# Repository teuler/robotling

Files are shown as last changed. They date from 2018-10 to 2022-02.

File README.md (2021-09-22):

# robotling

"robotling" is a simple circuit board to control small robots. Check out the videos (videos [1](https://youtu.be/wil41YtIeN8), [2](https://youtu.be/cLstXW3RsBA), [3](https://www.youtube.com/watch?v=XF0T9Dlb07M), and with thermal camera, [4](https://youtu.be/qpSQO51BuJs), [5](https://youtu.be/tlYXab0FZrY)) and find the details in the German [wiki](https://github.com/teuler/robotling/wiki). 

<p align="center">
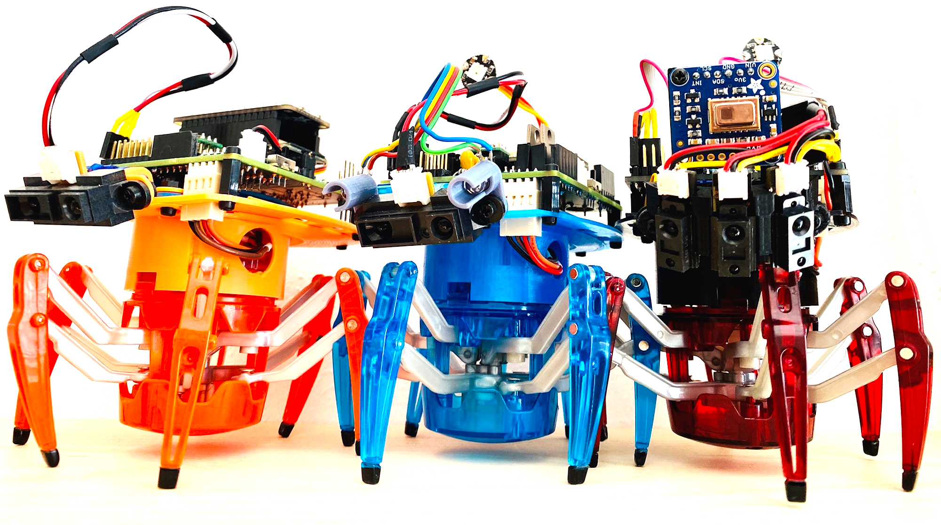
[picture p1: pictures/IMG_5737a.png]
  
</p>

### Release Notes

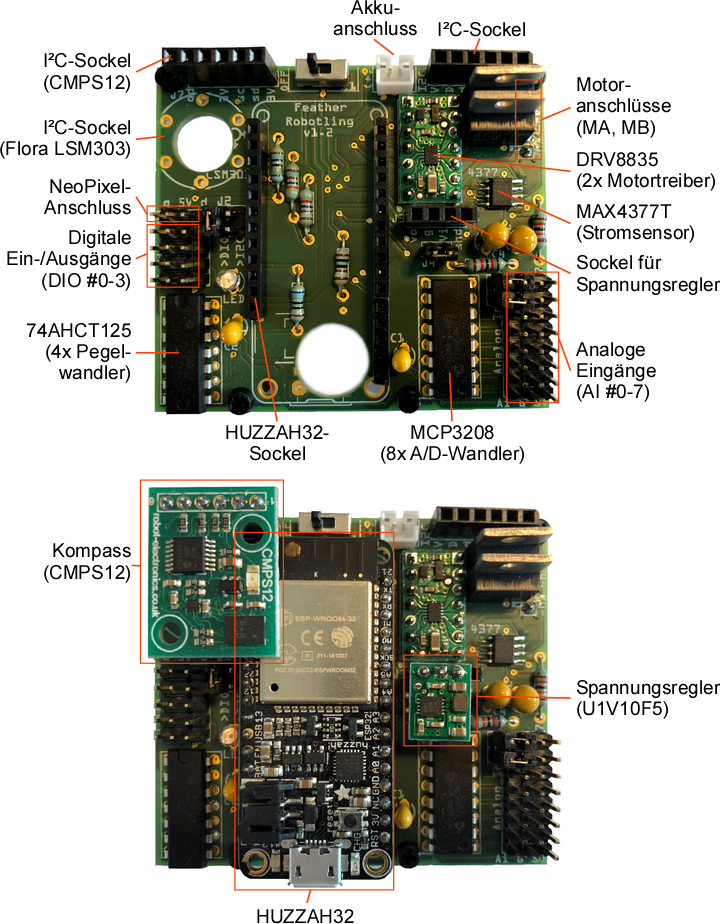
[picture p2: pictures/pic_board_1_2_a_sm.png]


* 2021-09-22
  - New firmware based on MicroPython v1.17 (w/`ulab`)
  - 
* 2021-05-02
  - Some refactoring: Configuration parameters now clearly marked as such (`cfg.xxx`)

* 2021-05-01 - Release v1.9

* 2021-04-26
  - [Instructions](https://github.com/teuler/robotling/wiki/Adding-native-modules-to-MicroPython-(ESP32)) for building MicroPython (release 1.14) w/`ulab` and `umqtt` updated. 
  - New pre-built ESP32 [firmware](https://github.com/teuler/robotling/tree/master/code/firmware_esp32) based on MicroPython v1.14 (w/`ulab` and `umqtt`)
  - Small bug fixes, now compatible w/ MicroPython v1.14 and "vanilla" v1.15 ([esp32-20210420-unstable-v1.15.bin](https://micropython.org/resources/firmware/esp32-20210420-unstable-v1.15.bin)).
  - Now uses `RobotlingBase` (from [`robotling_lib`](https://github.com/teuler/robotling_lib)), so better separate standard hardware and additional hardware defined in `devices` (in [hexbug_config.py](https://github.com/teuler/robotling/blob/master/code/robotling/hexbug_config.py)). 
  - As [`robotling_lib`](https://github.com/teuler/robotling_lib) now includes `simple.py` and `robust.py` from [micropython-lib](https://github.com/micropython/micropython-lib) as fall-back, MQTT can now be used with the standard MicroPython firmware, which does not inlcude `umqtt`.
  - Added [instructions](https://github.com/teuler/robotling/wiki/Adding-native-modules-to-MicroPython-(ESP32)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) how to build the ESP32 firmware for MicroPython 1.15 with `ulab` included. 

* 2021-04-05 
  - Link to new Make: article added. 
* 2020-08-30 (Blob detection revisited)
  - [Three versions](https://github.com/teuler/robotling/wiki/Verhalten#SeekBlob) of the blob detection and image filter code, demonstrating differences in speed between a pure MicroPython version and those that use [`ulab`](https://micropython-ulab.readthedocs.io/en/latest/ulab.html) or even user-written C functions added to `ulab`.
* 2020-08-21 (Refactoring)
  - Since it was difficult to maintain different versions of the robotling code all accessing the same set of driver etc. libraries, these files have now been moved to a separate repository ([`robotling_lib`](https://github.com/teuler/robotling_lib)). 
  - Wiki updated accordingly.
  - New Wiki page on [adding native modules to MicroPython](https://github.com/teuler/robotling/wiki/Adding-native-modules-to-MicroPython-(ESP32)).

* 2020-07-04 (Code updates)
  - Simple GUI to show robot status via MQTT (`hexbug.gui.py`) 
  - Support for [TinyPICO](https://www.tinypico.com/) added
  - Configurations for different hardware combinations
  - General class to manage and control a set of servos ([`servo_manager.py`](https://github.com/teuler/robotling/blob/master/code/robotling/motors/servo_manager.py)) and inprovements in Servo class
   - Class for [PCA9685 16-channel servo driver](https://www.adafruit.com/product/815) ([`servos_pca9685.py`](https://github.com/teuler/robotling/blob/master/code/robotling/motors/servos_pca9685.py))
   - Class for [18-channel Mini Maestro servo driver](https://www.pololu.com/product/1354) ([`servos_mini_maestro_18.py`](https://github.com/teuler/robotling/blob/master/code/robotling/motors/servos_mini_maestro_18.py))

* 2019-12-30 (requires MicroPython 1.12.x)
  - [Thermal camera](https://github.com/teuler/robotling/wiki/Sensoren-etc#AMG88XX) support added ([`amg88xx.py`](https://github.com/teuler/robotling/blob/master/code/robotling/driver/amg88xx.py) and [`camera_thermal.py`](https://github.com/teuler/robotling/blob/master/code/robotling/sensors/camera_thermal.py); new behaviour [`lookAtBlob`](https://github.com/teuler/robotling/wiki/Verhalten#SeekBlob) using the thermal camera (see videos [4](https://youtu.be/qpSQO51BuJs), [5](https://youtu.be/tlYXab0FZrY)). _Note that the blob detection (not the camera itself) requires a custom MicroPython [firmware](https://github.com/teuler/robotling/tree/master/code/firmware_esp32) that includes the module [`blob`](https://github.com/teuler/robotling/tree/master/code/modules/blob) (coded in C for speed reasons)._  
  - Configuration file split into fixed ([`hexbug_global.py`](https://github.com/teuler/robotling/blob/master/code/robotling/hexbug_global.py)) and robot-dependent definitions
  - Code adapted to MicroPython release 1.12.x, including hardware I2C bus option added and native code generation added for time critical routines (ESP32 only)
  - PWM frequencies for servos and DC motors are now defined in `robotling_board.py` to account for the fact that the ESP32 port supports only a single frequency for all standard PWM pins. In addition, [`drv8835.py`](https://github.com/teuler/robotling/blob/master/code/robotling/driver/drv8835.py) now uses the RMT feature of the ESP32 for PWM to run the DC motors. This allows using a different frequency than the normal PWM functions.

* 2019-11-15
  - New articel in the German Make: magazine (["Krabbelroboter sendet Telemetrie"](https://www.heise.de/select/make/2019/7/1573927054956141)). 
* 2019-08-31
  - New type of Sharp sensor added (GP2Y0AF15X, 1.5-15 cm) to `sensors\sharp_ir_ranging.py`. This allows using a triple IR distance sensor array such that the robot's head does not need to scan sideways.
  - I2C frequency increased to 400 kHz in `robotling_board.py`. The I2C frequency used is now also printed when the robot boots.
  - Robotling v1.3 board in `robotling_board_version.py`.
  - In case of an uncaught Python exception, the firmware tries to send a last MQTT message containing the traceback, allowing to get information on code errors even when the robot is not attached via USB.
  - Wiki page [Telemetrie über MQTT](https://github.com/teuler/robotling/wiki/Telemetrie-%C3%BCber-das-MQTT-Protokoll)
  
* 2019-07-25
  - Now an option was added to send telemetry via WLAN using the MQTT protocol (ESP32 only). An example script (`test_mqtt.py`) that demonstrates how to subcribe to robotling telemetry on a PC was added to `../code`. 
  - `hexbug.py` - Bias factor (`IR_SCAN_BIAS_F`) added to the configuration file `hexbug_config.py`; it allows correcting for a direction bias in the turning motor. Also, the scan scheme was slightly changed from "left-right-center" to "left-center-right-center", which helps the robot to walk more straight.
  - `telemetry.py`- Encapsules the MQTT functionality. 
  - `main.py` - Simple "memory" was added to remember the direction of successful turns (experimental).
  - `robotling.py` - Now the keyword "wlan" can be added as a device to `MORE_DEVICES` in `hexbug_config.py` to activate the network (instead of changing `boot.py`)
* 2019-07-22
  - Robotling code moved from `../code` to `../code/robotling`
* 2019-07-16 - Release v1.7
  - New wiki pages ['Sensors etc.'](https://github.com/teuler/robotling/wiki/Sensoren-etc) with supported sensors and ['Verhalten'](https://github.com/teuler/robotling/wiki/Verhalten) with behaviours added
  - Wiki pages ['Demo'](https://github.com/teuler/robotling/wiki/Demo) and ['Erweiterungen und Modifikationen'](https://github.com/teuler/robotling/wiki/Erweiterungen-und-Modifikationen) updated 
  - Code Release [v1.7](https://github.com/teuler/robotling/releases)
* 2019-05-18 - Release v1.6
  - Added new "behaviour" (take a nap) based on deepsleep/lightsleep support for ESP32
  - Cleaned up the code
  - Changed `hexbug_config.py`to make it also standard Python compatible (for future extension)
  - Now uses `getHeading3D` instead of `getPitchRoll` to determine if the robot is tilted; the additional 
    compass information (heading) is saved (for future extension).
  - Driver for LSM9DS0 magnetometer/accelerometer/gyroscope added.
* 2019-03-17 - Release v1.5
  - Some code improvements (handing devices, cleaning up)
  - Tested w/ MicroPython v1.10
  - New pictures
  - A new wiki page with extentions and modifications
* 2019-03-02
  - New pictures, annotated pictures of board v1.2
  - some new text on memory and performance
* 2019-01-12 
  - A few bug fixes
  - More drivers (dotstar, VL6180X). 
  - Works now also with the M4 Express Feather from Adafruit (and CircuitPython).
* 2018-12-28 - Release v1.3  
  Eliminated the need for a timer. Added `spin_ms()`, which needs to be called once per loop and instead of `sleep_ms()` to keep board
  updated. This solution is superior to the use of a timer, because (i) it is deterministic (avoids randomly interrupting the program 
  flow and, hence, inconsistencies) and (ii) makes the code compatible to CircuitPython, which does not (yet?) support timers.
* 2018-12-24 - Release v1.2  
  Now board v1.2 included, some code refactoring and improvements
* 2018-11-29 - Release v1.1  
  First complete version for board v1.0 and huzzah32
* 2018-11-18 - Initial release 

### Unresolved Issues

  - Tilt correction and calibration for LSM303 and LSM9DS0 compass function is not yet implemented.

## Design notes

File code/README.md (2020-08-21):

This folder contains python code that runs on a PC, e.g. to communicate with a robotling via WLAN, as well as hexbug/robotling configuration examples:  
- `test_mqtt.py` - Simple example script that illustrates how to receive MQTT telemetry from a robotling
- `hexbug_relay.py` Script that resends HexBug robotling MQTT messages under "proper" topics
- "Typical" configuration examples for different robotlings:
  - `hexbug_config.py__blue_1IR` - one IR distance sensor, WiFi, LSM9DS0-type compass
  - `hexbug_config.py__black3IR` - three [smaller IR sensors](https://github.com/teuler/robotling/wiki/Sensoren-etc#GP2Y0AF15X), WiFi, CMPS12-type compass, and an [AMG88XX GRID-Eye IR 8x8 thermal camera](https://learn.adafruit.com/adafruit-amg8833-8x8-thermal-camera-sensor?view=all) from Adafruit

The subfolder `robotling` contains the code that runs on the roboter.  

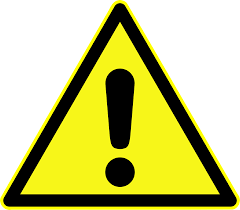
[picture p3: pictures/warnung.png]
[](https://github.com/teuler/robotling/blob/master/pictures/warnung.png)
**IMPORTANT: _The robotling code now relies on the drivers in [`robotling_lib`](https://github.com/teuler/robotling_lib), which has to be clones into the `robotling` 
  folder on the development PC._**

The folder `modules/blob` contains the C code for a simple module that takes a camera image (i.e. from the thermal camera), detects "blobs" and returns them as a list. This module has to be built into the Micropython firmware; see [notes](https://github.com/teuler/robotling/tree/master/code/modules/blob) in the `module/blob` folder.  

The subfolder `firmware` contains precompiled images of the current MicroPython firmware including `umqtt` and `blob`.

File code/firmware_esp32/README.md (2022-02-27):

## Pre-build firmware for the HUZZAH32 (ESP32):

- `esp32-idf4-20191229-v1.12_blob.bin` - Firmware based on MicroPython v1.12 w/ blob module 
- `esp32-idf3-20210418-v1.14_ulab.bin` - Firmware based on MicroPython v1.14 w/ [`ulab`](https://github.com/v923z/micropython-ulab)
- `esp32-idf4-20210501-v1.15_ulab.bin` - Firmware based on MicroPython v1.15 release w/ [`ulab`](https://github.com/v923z/micropython-ulab)
- `esp32-idf4-20210922-v1.17_ulab.bin` - Firmware based on MicroPython v1.17 release w/ [`ulab`](https://github.com/v923z/micropython-ulab), built w/ ESP-IDF v4.2.2

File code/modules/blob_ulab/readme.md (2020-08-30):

## Fast blob detection

Two functions for blob detection were added to the user module of [ulab](https://github.com/v923z/micropython-ulab): 

- `user.blob(img, dxy, nsd)` accepts an image (`img`), e.g. from the thermal camera, the image shape (`dxy` as 2-element tuple), and a threshold (`nsd`). The image must be an `nparray` (see [ulab](https://micropython-ulab.readthedocs.io/en/latest/index.html)). It then tries to detect "objects" (blobs, that is continuous areas with pixel values above the threshold), and returns a list of these objects. 
- `user.spatial_filter(img, kernel, dxy)` accepts an image (`img`) and a spatial kernel (`kernel`) as well as the image shape (`dxy` as 2-element tuple). The image and the kernel must be of the `nparray` type (see [ulab](https://micropython-ulab.readthedocs.io/en/latest/index.html)). The function convolves the image with the kernel and returns the filtered image.

For a code example, see [`blob_ulab2.py`](https://github.com/teuler/robotling_lib/blob/master/misc/blob_ulab2.py) and [`camera_thermal.py`](https://github.com/teuler/robotling_lib/blob/master/sensors/camera_thermal.py).

To acquire example images:
   ```
   import driver.amg88xx as amg88xx    # IR 8x8 thermal camera (AMG88XX) driver
   [...]
   AMG88XX = amg88xx.AMG88XX(I2C)      # with I2C being an initialized I2C bus instance
   [...]
   img = list(AMG88XX.pixels_64x1)
   ```
With `img` containing a single 8x8 frame from the thermal camera with a temperature values (°C) for each pixel, formated as a 1D list:
   ```
   [21, 21, 22, 23, 23, 21, 20, 20, 21, 21, 24, 24, 25, 22, 21, 21, 20, 21, 23, 25, 26, 25, 
    21, 21, 21, 21, 23, 26, 27, 26, 24, 22, 21, 22, 23, 25, 26, 28, 27, 28, 21, 21, 23, 26, 
    26, 26, 27, 26, 21, 21, 22, 23, 23, 23, 22, 23, 21, 22, 22, 21, 22, 21, 22, 23]
   ```
   
`blob.detect()` requires an image frame (as a linear list, see below), the frame size as a tuple (e.g. `(8,8)` for an 8x8 pixel frame) and a parameter tuple, consisting of the filter mode (`0`, no filter) and a threshold (`0.5`). The latter defines the number of standard deviations a blob maximum must higher that the mean frame intensity to be included as a valid blob.     
   ```
   import ulab as np
   from ulab import user
   [...]
   
   # Gaussian smooth
   np_kernel = np.array([[0.0625,0.125,0.0625], [0.125, 0.25, 0.125 ], [0.0625,0.125,0.0625]])
   np_img = np.array(img)
   dxy = (8, 8)
   nsp = 1.1
   np_imgf = user.spatial_filter(np_img, np_kernel, dxy)
   bloblist = user.blobs(np_imgf, dxy, nsp)
   ```
After blob detection - if blobs were found - `blobList` contains a list of blobs, with each blob represented by a tuple of blob area, index, probability (basically, a z-score), and blob center position in the frame:   
   ```
   [(13, 1, 0.6723409, 4.0, 4.846154)]
   ``` 

_**Important**: This code is preliminary and has not been fully optimized/debugged (see issues below)._

### Building the ESP32 MicroPython firmware with modified `ulab`

For a detailed description, see [here](https://github.com/teuler/robotling/wiki/Adding-native-modules-to-MicroPython-(ESP32)).

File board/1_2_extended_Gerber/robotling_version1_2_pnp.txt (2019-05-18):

*Pick And Place List
*Company=
*Author=
*eMail=
*
*Project=robotling_version1_2
*Date=15:33:05
*CreatedBy=Fritzing 0.9.3b.04.19.5c895d327c44a3114e5fcc9d8260daf0cbb52806
*
*
*Coordinates in mm, always center of component
*Origin 0/0=Lower left corner of PCB
*Rotation in degree (0-360, math. pos.)
*
*No;Value;Package;X;Y;Rotation;Side;Name
1;;;44.4293;-44.6364;0;Bottom;Via50
2;680;THT;24.1094;-18.6013;-90;Bottom;R4
3;;;28.5543;-53.5263;0;Bottom;Via48
4;;;13.9262;-52.2612;0;Bottom;Via75
5;;;29.1893;-37.0164;0;Bottom;Via40
6;;;32.375;-38.9205;0;Bottom;Via72
7;;THT;13.3144;-30.6663;90;Bottom;J2
8;;;19.3357;-53.3349;-90;Bottom;TXT1
9;;;47.7373;-53.331;-90;Bottom;TXT1
10;4.7µF;100 mil [THT, tantalum];55.8594;-28.1263;90;Bottom;C4
11;;;42.5243;-26.2214;0;Bottom;Via13
12;;;6.21718;-53.4393;-90;Bottom;TXT1
13;;;31.0943;-33.2064;0;Bottom;Via29
14;;;1.2007;-22.4621;-90;Bottom;TXT1
15;;;52.6035;-53.3492;-90;Bottom;TXT1
16;;;8.23426;-45.2714;0;Bottom;Hole14
17;;;59.0343;-39.5564;0;Bottom;Via58
18;;THT;62.8444;-47.1763;0;Bottom;Motors
19;;;65.4405;-44.3866;-90;Bottom;TXT1
20;;;62.8443;-33.8414;0;Bottom;Via61
21;;;14.7993;-26.7811;-90;Bottom;TXT1
22;;;22.3199;-55.7132;-90;Bottom;TXT1
23;;THT;47.6044;-31.9363;-90;Bottom;J3
24;;;6.9643;-20.5064;0;Bottom;Via36
25;;;35.5421;-57.3266;0;Bottom;Via64
26;;;19.6643;-38.9214;0;Bottom;Via69
27;;;33.6343;-21.7764;0;Bottom;Via8
28;;;29.1893;-38.9214;0;Bottom;Via65
29;1k;THT;31.7294;-24.3163;-90;Bottom;R5
30;;;61.5175;-0.866214;0;Bottom;TXT1
31;12k;THT;55.2244;-24.3163;180;Bottom;R10
32;4.7µF;100 mil [THT, tantalum];60.9394;-28.1263;90;Bottom;C3
33;;;43.7877;-29.169;-90;Bottom;TXT1
34;;;1.22046;-30.1829;-90;Bottom;TXT1
35;;;6.9643;-35.7464;0;Bottom;Via77
36;;DIP (Dual Inline) [THT];6.3294;-10.3463;0;Bottom;SN72AHCT125N
37;;THT;3.1544;-26.2213;0;Bottom;DIO_c
38;;THT;5.6944;-26.2213;0;Bottom;DIO_b
39;;;59.0343;-31.3014;0;Bottom;Via59
40;;DIP (Dual Inline) [THT];46.3344;-43.3663;0;Bottom;DRV8835
41;;;27.7523;-46.5775;0;Bottom;TXT1
42;;;12.161;-26.8012;-90;Bottom;TXT1
43;;;5.38164;-34.8472;0;Bottom;TXT1
44;;;29.8243;-8.44133;0;Bottom;Hole13
45;;3 mm [THT];13.3143;-22.3951;180;Bottom;LED1
46;;;64.1143;-56.0663;0;Bottom;Hole12
47;;THT;64.7494;-12.2513;180;Bottom;Analog_In_c
48;;;46.1595;-29.6662;-90;Bottom;TXT1
49;;;4.43446;-17.9616;0;Bottom;Via76
50;;THT;53.9544;-56.0663;-90;Bottom;I2C
51;;;50.237;-54.0079;-90;Bottom;TXT1
52;;;30.4593;-40.8264;0;Bottom;Via66
53;;;16.6298;-53.3869;-90;Bottom;TXT1
54;;;45.0643;-52.2563;0;Bottom;Via67
55;;THT;62.2094;-12.2513;180;Bottom;Analog_In_b
56;;;13.3137;-9.72549;0;Bottom;Via35
57;;;55.0686;-53.3576;-90;Bottom;TXT1
58;1µF;100 mil [THT, tantalum];13.9494;-14.1563;90;Bottom;C2
59;;;59.0335;-44.0011;0;Bottom;Via62
60;;;65.4718;-49.3365;-90;Bottom;TXT1
61;;;42.5243;-28.7614;0;Bottom;Via14
62;;;60.3172;-53.3197;-90;Bottom;TXT1
63;;;40.0012;-47.8249;0;Bottom;Via47
64;;THT;8.2344;-26.2213;0;Bottom;DIO
65;;THT;57.1294;-21.1413;0;Bottom;J5
66;;THT;59.6694;-12.2513;180;Bottom;Analog_In
67;;;49.0225;-29.4181;-90;Bottom;TXT1
68;;;27.9193;-29.6556;-90;Bottom;Feather
69;;;8.2344;-45.3983;180;Bottom;LSM303
70;;;14.5843;-2.09139;0;Bottom;Hole10
71;;so08;58.3233;-36.3813;90;Top;4377
72;;DIP (Dual Inline) [THT];49.5094;-12.2513;180;Bottom;MCP3208
73;;;31.0943;-37.6514;0;Bottom;Via2
74;;;36.1743;-31.9364;0;Bottom;Via28
75;;;38.7247;-52.8881;0;Bottom;Via68
76;;THT;5.6944;-32.5713;-90;Bottom;NP
77;;;41.2543;-33.8414;0;Bottom;Via11
78;8.2k;THT;23.4744;-37.6513;-90;Bottom;R2
79;;;40.6194;-56.0663;0;Bottom;LiPo Battery 1100 mAh
80;8.2k;THT;26.0144;-33.8413;-90;Bottom;R1
81;;;14.0449;-53.3946;-90;Bottom;TXT1
82;;;31.7293;-16.6964;0;Bottom;Via71
83;;switch-spdt;28.5543;-56.0663;-90;Bottom;S1
84;;;53.3193;-36.3814;0;Bottom;Via60
85;;;42.5243;-2.09139;0;Bottom;Hole9
86;;;50.779;-21.1513;0;Bottom;Via73
87;;THT;13.3144;-33.2063;90;Bottom;J2_b
88;;THT;57.1294;-18.6013;0;Bottom;J6
89;;;34.9043;-45.9064;0;Bottom;Via6
90;;;51.4547;-28.4762;-90;Bottom;TXT1
91;;;34.9043;-23.0464;0;Bottom;Via7
92;680;THT;20.9344;-40.8263;90;Bottom;R3
93;;THT;47.6044;-26.8563;90;Bottom;J4
94;0;THT;57.1294;-45.9063;0;Bottom;R8
95;;;64.9349;-23.098;-90;Bottom;TXT1
96;;;17.7593;-15.4264;0;Bottom;Via30
97;;;52.6705;-29.4054;0;Bottom;Via74
98;12k;THT;64.7494;-30.0313;90;Bottom;R9
99;;;36.3201;-55.9304;-90;Bottom;TXT1
100;;;53.3193;-52.8913;0;Bottom;Via63
101;;;2.51929;-56.0663;0;Bottom;Hole11
102;;;60.3043;-32.5714;0;Bottom;Via57
103;;;46.3343;-48.4464;0;Bottom;Via49
104;;;57.9151;-53.0828;-90;Bottom;TXT1
105;;THT;12.6794;-56.0663;-90;Bottom;J7
106;;;57.7643;-38.2864;0;Bottom;Via56
107;0;THT;57.1294;-50.9863;0;Bottom;R6
108;;;33.6343;-44.6364;0;Bottom;Via9
109;;;27.935;-48.4782;0;Bottom;TXT1
110;1µF;100 mil [THT, tantalum];41.8894;-9.07628;90;Bottom;C1
111;;;11.3164;-53.3499;-90;Bottom;TXT1

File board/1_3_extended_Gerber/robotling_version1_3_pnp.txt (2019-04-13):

*Pick And Place List
*Company=
*Author=
*eMail=
*
*Project=robotling_version1_3
*Date=15:26:20
*CreatedBy=Fritzing 0.9.3b.04.19.5c895d327c44a3114e5fcc9d8260daf0cbb52806
*
*
*Coordinates in mm, always center of component
*Origin 0/0=Lower left corner of PCB
*Rotation in degree (0-360, math. pos.)
*
*No;Value;Package;X;Y;Rotation;Side;Name
1;;;59.0086;-31.3014;0;Bottom;Via59
2;;THT;13.2887;-30.6663;90;Bottom;J2
3;;;42.4986;-2.09139;0;Bottom;Hole9
4;;;52.5778;-53.3492;-90;Bottom;TXT1
5;;so08;58.2976;-36.3813;90;Top;4377
6;12k;THT;55.1987;-24.3163;180;Bottom;R10
7;;;40.5937;-56.0663;0;Bottom;LiPo Battery 1100 mAh
8;;;33.6086;-42.7314;0;Bottom;Via9
9;;;48.9968;-29.4181;-90;Bottom;TXT1
10;4.7µF;100 mil [THT, tantalum];60.9137;-28.1263;90;Bottom;C3
11;;DIP (Dual Inline) [THT];6.30372;-10.3463;0;Bottom;SN72AHCT125N
12;;;27.8936;-29.6556;-90;Bottom;Feather
13;;;12.1354;-26.8012;-90;Bottom;TXT1
14;;;14.5586;-2.09139;0;Bottom;Hole10
15;;;41.2286;-33.8414;0;Bottom;Via11
16;;;65.4462;-49.3365;-90;Bottom;TXT1
17;;;34.8786;-23.0464;0;Bottom;Via7
18;1k;THT;27.8937;-19.8713;-90;Bottom;R5
19;;THT;64.7237;-12.2513;180;Bottom;Analog_In_c
20;;THT;8.20872;-26.2213;0;Bottom;DIO
21;;;39.9756;-47.8249;0;Bottom;Via47
22;;;1.17502;-22.4621;-90;Bottom;TXT1
23;;;13.9005;-52.2612;0;Bottom;Via75
24;;;6.1915;-53.4393;-90;Bottom;TXT1
25;;;38.6991;-52.8881;0;Bottom;Via68
26;;;30.4336;-40.8264;0;Bottom;Via66
27;;;61.4918;-0.866214;0;Bottom;TXT1
28;;THT;59.6437;-12.2513;180;Bottom;Analog_In
29;;;8.20858;-45.2714;0;Bottom;Hole14
30;;;14.6398;-53.3946;-90;Bottom;TXT1
31;;;1.19478;-30.1829;-90;Bottom;TXT1
32;;;13.2881;-9.72549;0;Bottom;Via35
33;;;36.1486;-31.9364;0;Bottom;Via28
34;;;59.0078;-44.0011;0;Bottom;Via62
35;;THT;47.5787;-31.9363;-90;Bottom;J3
36;;THT;5.66872;-26.2213;0;Bottom;DIO_b
37;;THT;53.9287;-56.0663;-90;Bottom;I2C
38;;;27.7266;-46.5775;0;Bottom;TXT1
39;;;22.2943;-55.7132;-90;Bottom;TXT1
40;;;4.40878;-17.9616;0;Bottom;Via76
41;;THT;47.5787;-26.8563;90;Bottom;J4
42;;;33.6486;-23.0199;-90;Bottom;TXT1
43;;THT;5.66872;-32.5713;-90;Bottom;NP
44;;;5.35596;-34.8472;0;Bottom;TXT1
45;;;52.6448;-29.4054;0;Bottom;Via74
46;;THT;31.0687;-25.5863;180;Bottom;J9
47;0;THT;57.1037;-45.9063;0;Bottom;R8
48;680;THT;20.9087;-40.8263;90;Bottom;R3
49;;;11.9113;-53.3499;-90;Bottom;TXT1
50;1µF;100 mil [THT, tantalum];13.9237;-14.1563;90;Bottom;C2
51;;switch-spdt;28.5286;-56.0663;-90;Bottom;S1
52;;;47.7116;-53.331;-90;Bottom;TXT1
53;;;42.4986;-26.2214;0;Bottom;Via13
54;;;64.9093;-23.098;-90;Bottom;TXT1
55;;;6.93862;-20.5064;0;Bottom;Via36
56;;;29.1636;-37.0164;0;Bottom;Via40
57;;;17.2247;-53.3869;-90;Bottom;TXT1
58;;;27.9093;-48.4782;0;Bottom;TXT1
59;;;34.8786;-45.9064;0;Bottom;Via6
60;;THT;13.2887;-33.2063;90;Bottom;J2_b
61;;;43.7621;-29.169;-90;Bottom;TXT1
62;;;60.2786;-32.5714;0;Bottom;Via57
63;;THT;62.8187;-47.1763;0;Bottom;Motors
64;;;65.4148;-44.3866;-90;Bottom;TXT1
65;;;31.0686;-33.2064;0;Bottom;Via29
66;;;44.4036;-44.6364;0;Bottom;Via50
67;;;19.9306;-53.3349;-90;Bottom;TXT1
68;;;57.8894;-53.0828;-90;Bottom;TXT1
69;;;45.0386;-52.2563;0;Bottom;Via67
70;;THT;57.1037;-21.1413;0;Bottom;J5
71;8.2k;THT;23.4487;-37.6513;-90;Bottom;R2
72;4.7µF;100 mil [THT, tantalum];55.8337;-28.1263;90;Bottom;C4
73;;DIP (Dual Inline) [THT];49.4837;-12.2513;180;Bottom;MCP3208
74;;;59.0086;-39.5564;0;Bottom;Via58
75;;;55.0429;-53.3576;-90;Bottom;TXT1
76;;3 mm [THT];13.2886;-22.3951;180;Bottom;LED1
77;;;53.2936;-36.3814;0;Bottom;Via60
78;;;6.93862;-35.7464;0;Bottom;Via77
79;;;64.0886;-56.0663;0;Bottom;Hole12
80;;;51.429;-28.4762;-90;Bottom;TXT1
81;;THT;62.1837;-12.2513;180;Bottom;Analog_In_b
82;;;30.4337;-7.80633;0;Bottom;Hole13
83;;DIP (Dual Inline) [THT];46.3087;-43.3663;0;Bottom;DRV8835
84;;;36.2945;-55.9304;-90;Bottom;TXT1
85;;;32.3493;-38.9205;0;Bottom;Via72
86;;THT;31.0687;-20.5063;180;Bottom;J8
87;;;17.7336;-15.4264;0;Bottom;Via30
88;;;50.2113;-54.0079;-90;Bottom;TXT1
89;;;2.49361;-56.0663;0;Bottom;Hole11
90;8.2k;THT;25.9887;-33.8413;-90;Bottom;R1
91;0;THT;57.1037;-50.9863;0;Bottom;R6
92;;;42.4986;-28.7614;0;Bottom;Via14
93;;;35.5164;-57.3266;0;Bottom;Via64
94;;THT;13.2887;-56.0663;-90;Bottom;J7
95;;;31.0686;-37.6514;0;Bottom;Via2
96;12k;THT;64.7237;-30.0313;90;Bottom;R9
97;;;7.95472;-45.5253;180;Bottom;LSM303
98;;;28.5286;-53.5263;0;Bottom;Via48
99;;;50.7533;-21.1513;0;Bottom;Via73
100;;;46.3086;-48.4464;0;Bottom;Via49
101;;;46.1338;-29.6662;-90;Bottom;TXT1
102;;;57.7386;-38.2864;0;Bottom;Via56
103;680;THT;24.0837;-18.6013;-90;Bottom;R4
104;1µF;100 mil [THT, tantalum];41.8637;-9.07628;90;Bottom;C1
105;;;29.1636;-38.9214;0;Bottom;Via65
106;;;53.2936;-52.8913;0;Bottom;Via63
107;;;60.2915;-53.3197;-90;Bottom;TXT1
108;;;19.6386;-38.9214;0;Bottom;Via69
109;;THT;3.12872;-26.2213;0;Bottom;DIO_c
110;;THT;57.1037;-18.6013;0;Bottom;J6
111;;;14.7736;-26.7811;-90;Bottom;TXT1
112;;;62.8186;-33.8414;0;Bottom;Via61

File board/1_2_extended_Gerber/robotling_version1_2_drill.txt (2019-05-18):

; NON-PLATED HOLES START AT T1
; THROUGH (PLATED) HOLES START AT T100
M48
INCH
T1C0.393700
T2C0.472440
T100C0.015748
T101C0.030000
T102C0.098425
T103C0.094488
T104C0.035000
T105C0.038000
T106C0.031497
T107C0.027559
T108C0.040000
T109C0.035433
T110C0.047244
T111C0.031496
%
T1
X003241Y017823
T2
X011741Y003323
T100
X024741Y013323
X013241Y008573
X005241Y003828
X002741Y008073
X020736Y011576
X018241Y019073
X022741Y015073
X013741Y009073
X005482Y020575
X019991Y008327
X020991Y020823
X023741Y012823
X014241Y012573
X012241Y014823
X011991Y016073
X011241Y021073
X020991Y014323
X016241Y013323
X016741Y011323
X015246Y020822
X023241Y012323
X015748Y018828
X007741Y015323
X016741Y010323
X023241Y015573
X011491Y014573
X023241Y017323
X017741Y020573
X013741Y018073
X012241Y013073
X006991Y006073
X013241Y017573
X011491Y015323
X017491Y017573
X013993Y022569
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

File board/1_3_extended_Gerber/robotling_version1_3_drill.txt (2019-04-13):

; NON-PLATED HOLES START AT T1
; THROUGH (PLATED) HOLES START AT T100
M48
INCH
T1C0.472440
T2C0.393700
T100C0.031496
T101C0.027559
T102C0.035000
T103C0.094488
T104C0.015748
T105C0.098425
T106C0.031497
T107C0.038000
T108C0.047244
T109C0.040000
T110C0.030000
T111C0.035433
%
T1
X011981Y003073
T2
X003231Y017823
T100
X012281Y002677
X009682Y002677
T101
X003981Y003073
X000981Y007073
X000981Y006073
X003981Y001073
X000981Y004073
X000981Y001073
X003981Y005073
X003981Y004073
X000981Y005073
X000981Y002073
X000981Y003073
X003981Y007073
X003981Y002073
X003981Y006073
T102
X019731Y014073
X017981Y004323
X019731Y009573
X017981Y001323
X016731Y014073
X017981Y003323
X019731Y017073
X020981Y003323
X008231Y018073
X019731Y020073
X020981Y007323
X021481Y018073
X017981Y002323
X010231Y015323
X016731Y018073
X021481Y020073
X010231Y011323
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

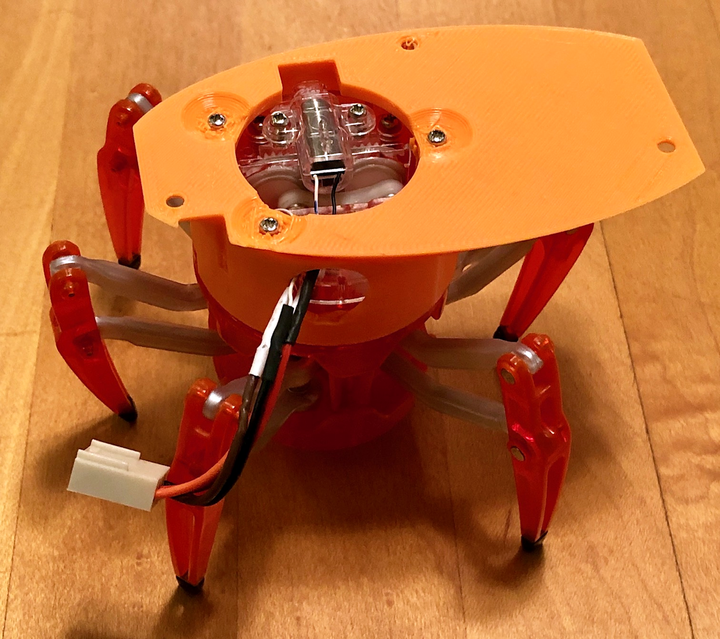
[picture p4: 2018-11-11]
pictures/IMG_4534_sm.png

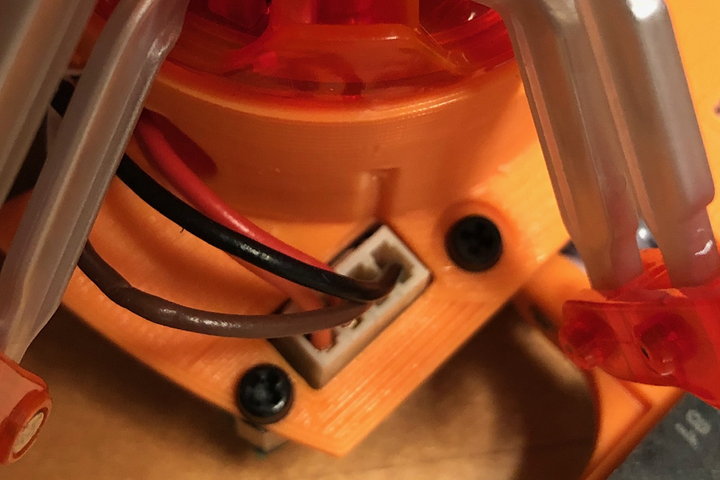
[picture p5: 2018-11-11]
pictures/IMG_4548_sm.png

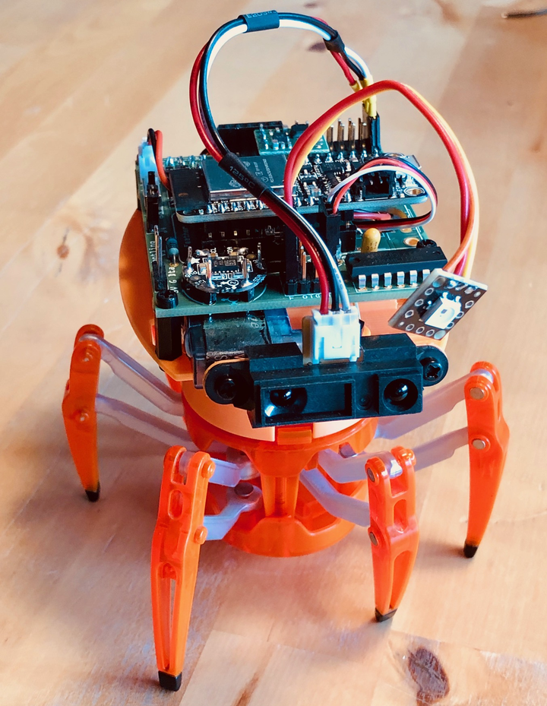
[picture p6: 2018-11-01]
pictures/IMG_4510_sm.png

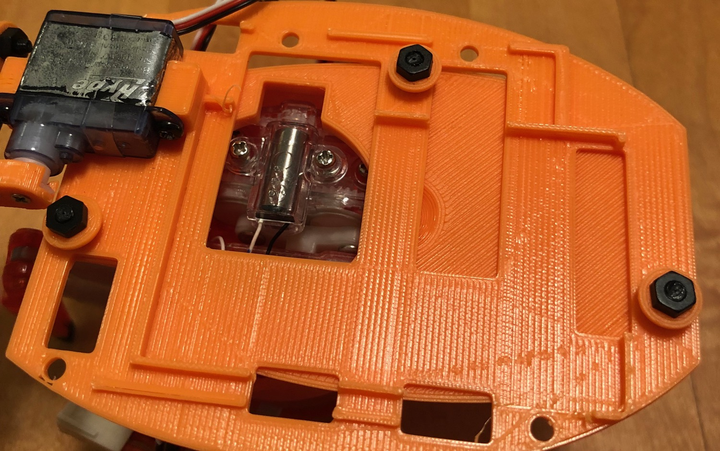
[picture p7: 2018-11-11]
pictures/IMG_4541_sm.png

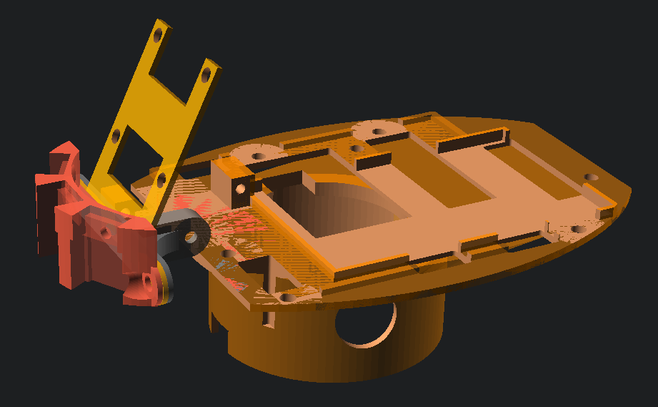
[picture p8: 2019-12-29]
pictures/arm_w_camera_holder.png

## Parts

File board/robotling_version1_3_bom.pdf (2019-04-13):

# Bill of Materials: robotling_version1_3.fzz

D:/User/Dropbox/__ROS/__Circuit boards/board_robotling/robotling_version1_3.fzz
Samstag, April 13 2019, 15:27:31

# Assembly List

Label | Part Type | Properties
4377 | MAX4377T | Variante variant 1; Paket so08
Analog_In | Generic female header -
| 8 pins | Lochgröße 1.0mm,0.508mm; Beinchen 8; Paket THT;
| | Beinchenabstand 0.1in (2.54mm); row single; Form ♀
| | (female)
Analog_In_b | Generic female header -
| 8 pins | Lochgröße 1.0mm,0.508mm; Beinchen 8; Paket THT;
| | Beinchenabstand 0.1in (2.54mm); row single; Form ♀
| | (female)
Analog_In_c | Generic female header -
| 8 pins | Lochgröße 1.0mm,0.508mm; Beinchen 8; Paket THT;
| | Beinchenabstand 0.1in (2.54mm); row single; Form ♀
| | (female)
C1 | Tantalum Capacitor | Spannung 6.3V; Paket 100 mil [THT, tantalum]; Kapazität
| | 1μF
C2 | Tantalum Capacitor | Spannung 6.3V; Paket 100 mil [THT, tantalum]; Kapazität
| | 1μF
C3 | Tantalum Capacitor | Spannung 16V; Paket 100 mil [THT, tantalum]; Kapazität
| | 4.7µF
C4 | Tantalum Capacitor | Spannung 16V; Paket 100 mil [THT, tantalum]; Kapazität
| | 4.7µF
DIO | Generic female header -
| 4 pins | Lochgröße 1.0mm,0.508mm; Beinchen 4; Paket THT;
| | Beinchenabstand 0.1in (2.54mm); row single; Form ♀
| | (female)
DIO_b | Generic female header -
| 4 pins | Lochgröße 1.0mm,0.508mm; Beinchen 4; Paket THT;
| | Beinchenabstand 0.1in (2.54mm); row single; Form ♀
| | (female)
DIO_c | Generic female header -
| 4 pins | Lochgröße 1.0mm,0.508mm; Beinchen 4; Paket THT;
| | Beinchenabstand 0.1in (2.54mm); row single; Form ♀
| | (female)
DRV8835 | DRV8835 | editable pin labels false; Variante variant 1; Beinchen 14;
| | Paket DIP (Dual Inline) [THT]; Beinchenabstand 300mil;
| | chip label DRV8835
Feather | Adafruit HUZZAH32
| ESP32 Feather | Variante variant 1; Bauteilnummer Adafruit #3405
I2C | Generic female header -
| 6 pins | Lochgröße 1.0mm,0.508mm; Beinchen 6; Paket THT;
| | Beinchenabstand 0.1in (2.54mm); row single; Form ♀
| | (female)
J2 | Generic male header - 2
| pins | Lochgröße 1.0mm,0.508mm; Beinchen 2; Paket THT;
| | Beinchenabstand 0.1in (2.54mm); row single; Form ♂
| | (male)
Fritzing Bill of Materials | file:///D:/User/Dropbox/__GIT/robotling/board/robotling_version1_3...
1 von 4 | 13.04.2019, 15:27

Label | Part Type | Properties
J2_b | Generic male header - 2
| pins | Lochgröße 1.0mm,0.508mm; Beinchen 2; Paket THT;
| | Beinchenabstand 0.1in (2.54mm); row single; Form ♂
| | (male)
J3 | Generic rounded female
| header - 4 pins | Lochgröße 1.0mm,0.508mm; Beinchen 4; Paket THT;
| | Beinchenabstand 0.1in (2.54mm); row single; Form ♀
| | (female rounded)
J4 | Generic female header -
| 2 pins | Lochgröße 1.0mm,0.508mm; Beinchen 2; Paket THT;
| | Beinchenabstand 0.1in (2.54mm); row single; Form ♀
| | (female)
J5 | Generic female header -
| 1 pins | Lochgröße 1.0mm,0.508mm; Beinchen 1; Paket THT;
| | Beinchenabstand 0.1in (2.54mm); row single; Form ♀
| | (female)
J6 | Generic female header -
| 1 pins | Lochgröße 1.0mm,0.508mm; Beinchen 1; Paket THT;
| | Beinchenabstand 0.1in (2.54mm); row single; Form ♀
| | (female)
J7 | Generic female header -
| 6 pins | Lochgröße 1.0mm,0.508mm; Beinchen 6; Paket THT;
| | Beinchenabstand 0.1in (2.54mm); row single; Form ♀
| | (female)
J8 | Generic female header -
| 2 pins | Lochgröße 1.0mm,0.508mm; Beinchen 2; Paket THT;
| | Beinchenabstand 0.1in (2.54mm); row single; Form ♀
| | (female)
J9 | Generic female header -
| 2 pins | Lochgröße 1.0mm,0.508mm; Beinchen 2; Paket THT;
| | Beinchenabstand 0.1in (2.54mm); row single; Form ♀
| | (female)
LED1 | Green (565nm) LED | Paket 3 mm [THT]; leg yes; Farbe Green (565nm)
LiPo Battery 1100 mAh | Lithium Ion Polymer
| Battery 3.7v 350mAh | Variante 350mAh; Bauteilnummer 2750
LSM303 | Flora LSM303
| Compass+Accel | Variante variant 1
MCP3208 | MCP3208 | true; Lochgröße 1.0mm,0.508mm; Beinchen 16; Paket DIP
| | (Dual Inline) [THT]; Beinchenabstand 300mil; Chip-
| | Beschriftung MCP3208
Motors | Generic female header -
| 4 pins | Lochgröße 1.0mm,0.508mm; Beinchen 4; Paket THT;
| | Beinchenabstand 0.1in (2.54mm); row single; Form ♀
| | (female); Bauteilnummer Motor connector
NP | Generic female header -
| 3 pins | Lochgröße 1.0mm,0.508mm; Beinchen 3; Paket THT;
| | Beinchenabstand 0.1in (2.54mm); row single; Form ♀
| | (female)
R1 | 8.2kΩ Resistor | bands 4; Widerstand 8.2kΩ; Paket THT; Beinchenabstand
| | 400 mil; Toleranz ±5%
R2 | 8.2kΩ Resistor | bands 4; Widerstand 8.2kΩ; Paket THT; Beinchenabstand
| | 400 mil; Toleranz ±5%
R3 | 680Ω Resistor | bands 4; Widerstand 680Ω; Paket THT; Beinchenabstand
| | 400 mil; Toleranz ±5%
R4 | 680Ω Resistor | bands 4; Widerstand 680Ω; Paket THT; Beinchenabstand
| | 400 mil; Toleranz ±5%
2 von 4 | 13.04.2019, 15:27

Label | Part Type | Properties
R5 | 1kΩ Resistor | bands 4; Widerstand 1kΩ; Paket THT; Beinchenabstand 400 mil; Toleranz ±5%
R6 | 0Ω Resistor | bands 4; Widerstand 0Ω; Paket THT; Beinchenabstand 400 mil; Toleranz ±5%
R8 | 0Ω Resistor | bands 4; Widerstand 0Ω; Paket THT; Beinchenabstand 400 mil; Toleranz ±5%
R9 | 12kΩ Resistor | bands 4; Widerstand 12kΩ; Paket THT; Beinchenabstand 400 mil; Toleranz ±5%
R10 | 12kΩ Resistor | bands 4; Widerstand 12kΩ; Paket THT; Beinchenabstand 400 mil; Toleranz ±5%
S1 | SPST Switch | Variante pth; Paket switch-spdt
SN72AHCT125N | SN72AHCT
| | true; Lochgröße 0.7mm,0.508mm; Beinchen 14; Paket DIP (Dual Inline) [THT]; Beinchenabstand 300mil; Chip- Beschriftung SN72AHCT

# Shopping List

Amount | Part Type | Properties
1 | MAX4377T | Variante variant 1; Paket so08

### 3 Generic female header - 8

| pins | Lochgröße 1.0mm,0.508mm; Beinchen 8; Paket THT; Beinchenabstand 0.1in (2.54mm); row single; Form ♀ (female)
2 | Tantalum Capacitor | Spannung 6.3V; Paket 100 mil [THT, tantalum]; Kapazität 1μF
2 | Tantalum Capacitor | Spannung 16V; Paket 100 mil [THT, tantalum]; Kapazität 4.7µF

### 3 Generic female header - 4

| pins | Lochgröße 1.0mm,0.508mm; Beinchen 4; Paket THT; Beinchenabstand 0.1in (2.54mm); row single; Form ♀ (female)
1 | DRV8835 | editable pin labels false; Variante variant 1; Beinchen 14; Paket DIP (Dual Inline) [THT]; Beinchenabstand 300mil; chip label DRV8835

### 1 Adafruit HUZZAH32

| ESP32 Feather | Variante variant 1; Bauteilnummer Adafruit #3405

### 2 Generic female header - 6

| pins | Lochgröße 1.0mm,0.508mm; Beinchen 6; Paket THT; Beinchenabstand 0.1in (2.54mm); row single; Form ♀ (female)

### 2 Generic male header - 2

| pins | Lochgröße 1.0mm,0.508mm; Beinchen 2; Paket THT; Beinchenabstand 0.1in (2.54mm); row single; Form ♂ (male)

### 1 Generic rounded female

| header - 4 pins | Lochgröße 1.0mm,0.508mm; Beinchen 4; Paket THT; Beinchenabstand 0.1in (2.54mm); row single; Form ♀ (female rounded)

### 3 Generic female header - 2

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

### 2 Generic female header - 1

| pins | Lochgröße 1.0mm,0.508mm; Beinchen 1; Paket THT; Beinchenabstand 0.1in (2.54mm); row single; Form ♀ (female)
3 von 4 | 13.04.2019, 15:27

Amount | Part Type | Properties
1 | Green (565nm) LED | Paket 3 mm [THT]; leg yes; Farbe Green (565nm)

### 1 Lithium Ion Polymer

| Battery 3.7v 350mAh | Variante 350mAh; Bauteilnummer 2750

### 1 Flora LSM303

| Compass+Accel | Variante variant 1
1 | MCP3208 | true; Lochgröße 1.0mm,0.508mm; Beinchen 16; Paket DIP (Dual Inline) [THT]; Beinchenabstand 300mil; Chip-Beschriftung MCP3208

### 1 Generic female header - 4

| pins | Lochgröße 1.0mm,0.508mm; Beinchen 4; Paket THT; Beinchenabstand 0.1in (2.54mm); row single; Form ♀ (female); Bauteilnummer Motor connector

### 1 Generic female header - 3

| pins | Lochgröße 1.0mm,0.508mm; Beinchen 3; Paket THT; Beinchenabstand 0.1in (2.54mm); row single; Form ♀ (female)
2 | 8.2kΩ Resistor | bands 4; Widerstand 8.2kΩ; Paket THT; Beinchenabstand 400 mil; Toleranz ±5%
2 | 680Ω Resistor | bands 4; Widerstand 680Ω; Paket THT; Beinchenabstand 400 mil; Toleranz ±5%
1 | 1kΩ Resistor | bands 4; Widerstand 1kΩ; Paket THT; Beinchenabstand 400 mil; Toleranz ±5%
2 | 0Ω Resistor | bands 4; Widerstand 0Ω; Paket THT; Beinchenabstand 400 mil; Toleranz ±5%
2 | 12kΩ Resistor | bands 4; Widerstand 12kΩ; Paket THT; Beinchenabstand 400 mil; Toleranz ±5%
1 | SPST Switch | Variante pth; Paket switch-spdt

### 1 SN72AHCT

| | true; Lochgröße 0.7mm,0.508mm; Beinchen 14; Paket DIP (Dual Inline) [THT]; Beinchenabstand 300mil; Chip-Beschriftung SN72AHCT

Exported with Fritzing 0.9.3- http://fritzing.org

4 von 4 | 13.04.2019, 15:27

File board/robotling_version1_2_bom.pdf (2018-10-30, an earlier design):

# Bill of Materials: robotling_version1_2.fzz

D:/User/Dropbox/__ROS/__Circuit boards/board_robotling/robotling_version1_2.fzz
Sonntag, Oktober 28 2018, 11:34:59

# Assembly List

Label | Part Type | Properties
4377 | MAX4377T | Paket so08; Variante variant 1
Analog_In | Generic female header -
| 8 pins | Form ♀ (female); row single; Paket THT; Beinchen 8;
| | Lochgröße 1.0mm,0.508mm; Beinchenabstand 0.1in
| | (2.54mm)
Analog_In_b | Generic female header -
| 8 pins | Form ♀ (female); row single; Paket THT; Beinchen 8;
| | Lochgröße 1.0mm,0.508mm; Beinchenabstand 0.1in
| | (2.54mm)
Analog_In_c | Generic female header -
| 8 pins | Form ♀ (female); row single; Paket THT; Beinchen 8;
| | Lochgröße 1.0mm,0.508mm; Beinchenabstand 0.1in
| | (2.54mm)
C1 | Tantalum Capacitor | Kapazität 1μF; Paket 100 mil [THT, tantalum]; Spannung
| | 6.3V
C2 | Tantalum Capacitor | Kapazität 1μF; Paket 100 mil [THT, tantalum]; Spannung
| | 6.3V
C3 | Tantalum Capacitor | Kapazität 4.7µF; Paket 100 mil [THT, tantalum]; Spannung
| | 16V
C4 | Tantalum Capacitor | Kapazität 4.7µF; Paket 100 mil [THT, tantalum]; Spannung
| | 16V
DIO | Generic female header -
| 4 pins | Form ♀ (female); row single; Paket THT; Beinchen 4;
| | Lochgröße 1.0mm,0.508mm; Beinchenabstand 0.1in
| | (2.54mm)
DIO_b | Generic female header -
| 4 pins | Form ♀ (female); row single; Paket THT; Beinchen 4;
| | Lochgröße 1.0mm,0.508mm; Beinchenabstand 0.1in
| | (2.54mm)
DIO_c | Generic female header -
| 4 pins | Form ♀ (female); row single; Paket THT; Beinchen 4;
| | Lochgröße 1.0mm,0.508mm; Beinchenabstand 0.1in
| | (2.54mm)
DRV8835 | DRV8835 | editable pin labels false; Paket DIP (Dual Inline) [THT];
| | Variante variant 1; Beinchen 14; chip label DRV8835;
| | Beinchenabstand 300mil
Feather | Adafruit HUZZAH32
| ESP32 Feather | Variante variant 1; Bauteilnummer Adafruit #3405
I2C | Generic female header -
| 6 pins | Form ♀ (female); row single; Paket THT; Beinchen 6;
| | Lochgröße 1.0mm,0.508mm; Beinchenabstand 0.1in
| | (2.54mm)
J2 | Generic male header - 2
| pins | Form ♂ (male); row single; Paket THT; Beinchen 2;
| | Lochgröße 1.0mm,0.508mm; Beinchenabstand 0.1in
| | (2.54mm)
Fritzing Bill of Materials | file:///D:/User/Dropbox/__ROS/__Circuit boards/board_robotling/robo...
1 von 4 | 28.10.2018, 11:43

Label | Part Type | Properties
J2_b | Generic male header - 2
| pins | Form ♂ (male); row single; Paket THT; Beinchen 2;
| | Lochgröße 1.0mm,0.508mm; Beinchenabstand 0.1in
| | (2.54mm)
J3 | Generic rounded female
| header - 4 pins | Form ♀ (female rounded); row single; Paket THT;
| | Beinchen 4; Lochgröße 1.0mm,0.508mm; Beinchenabstand
| | 0.1in (2.54mm)
J4 | Generic female header -
| 2 pins | Form ♀ (female); row single; Paket THT; Beinchen 2;
| | Lochgröße 1.0mm,0.508mm; Beinchenabstand 0.1in
| | (2.54mm)
J5 | Generic female header -
| 1 pins | Form ♀ (female); row single; Paket THT; Beinchen 1;
| | Lochgröße 1.0mm,0.508mm; Beinchenabstand 0.1in
| | (2.54mm)
J6 | Generic female header -
| 1 pins | Form ♀ (female); row single; Paket THT; Beinchen 1;
| | Lochgröße 1.0mm,0.508mm; Beinchenabstand 0.1in
| | (2.54mm)
J7 | Generic female header -
| 6 pins | Form ♀ (female); row single; Paket THT; Beinchen 6;
| | Lochgröße 1.0mm,0.508mm; Beinchenabstand 0.1in
| | (2.54mm)
LED1 | Green (565nm) LED | Paket 3 mm [THT]; Farbe Green (565nm); leg yes
LiPo Battery 1100 mAh | Lithium Ion Polymer
| Battery 3.7v 350mAh | Variante 350mAh; Bauteilnummer 2750
LSM303 | Flora LSM303
| Compass+Accel | Variante variant 1
MCP3208 | MCP3208 | true; Paket DIP (Dual Inline) [THT]; Beinchen 16;
| | Lochgröße 1.0mm,0.508mm; Chip-Beschriftung MCP3208;
| | Beinchenabstand 300mil
Motors | Generic female header -
| 4 pins | Form ♀ (female); row single; Paket THT; Beinchen 4;
| | Lochgröße 1.0mm,0.508mm; Beinchenabstand 0.1in
| | (2.54mm); Bauteilnummer Motor connector
NP | Generic female header -
| 3 pins | Form ♀ (female); row single; Paket THT; Beinchen 3;
| | Lochgröße 1.0mm,0.508mm; Beinchenabstand 0.1in
| | (2.54mm)
R1 | 8.2kΩ Resistor | Toleranz ±5%; Paket THT; bands 4; Widerstand 8.2kΩ;
| | Beinchenabstand 400 mil
R2 | 8.2kΩ Resistor | Toleranz ±5%; Paket THT; bands 4; Widerstand 8.2kΩ;
| | Beinchenabstand 400 mil
R3 | 680Ω Resistor | Toleranz ±5%; Paket THT; bands 4; Widerstand 680Ω;
| | Beinchenabstand 400 mil
R4 | 680Ω Resistor | Toleranz ±5%; Paket THT; bands 4; Widerstand 680Ω;
| | Beinchenabstand 400 mil
R5 | 1kΩ Resistor | Toleranz ±5%; Paket THT; bands 4; Widerstand 1kΩ;
| | Beinchenabstand 400 mil
R6 | 0Ω Resistor | Toleranz ±5%; Paket THT; bands 4; Widerstand 0Ω;
| | Beinchenabstand 400 mil
R8 | 0Ω Resistor | Toleranz ±5%; Paket THT; bands 4; Widerstand 0Ω;
| | Beinchenabstand 400 mil
2 von 4 | 28.10.2018, 11:43

Label | Part Type | Properties
R9 | 12kΩ Resistor | Toleranz ±5%; Paket THT; bands 4; Widerstand 12kΩ; Beinchenabstand 400 mil
R10 | 12kΩ Resistor | Toleranz ±5%; Paket THT; bands 4; Widerstand 12kΩ; Beinchenabstand 400 mil
S1 | SPST Switch | Paket switch-spdt; Variante pth
SN72AHCT125N | SN72AHCT
| | true; Paket DIP (Dual Inline) [THT]; Beinchen 14; Lochgröße 0.7mm,0.508mm; Chip-Beschriftung SN72AHCT; Beinchenabstand 300mil

# Shopping List

Amount | Part Type | Properties
1 | MAX4377T | Paket so08; Variante variant 1

### 3 Generic female header - 8

| pins | Form ♀ (female); row single; Paket THT; Beinchen 8; Lochgröße 1.0mm,0.508mm; Beinchenabstand 0.1in (2.54mm)
2 | Tantalum Capacitor | Kapazität 1μF; Paket 100 mil [THT, tantalum]; Spannung 6.3V
2 | Tantalum Capacitor | Kapazität 4.7µF; Paket 100 mil [THT, tantalum]; Spannung 16V

### 3 Generic female header - 4

| pins | Form ♀ (female); row single; Paket THT; Beinchen 4; Lochgröße 1.0mm,0.508mm; Beinchenabstand 0.1in (2.54mm)
1 | DRV8835 | editable pin labels false; Paket DIP (Dual Inline) [THT]; Variante variant 1; Beinchen 14; chip label DRV8835; Beinchenabstand 300mil

### 1 Adafruit HUZZAH32

| ESP32 Feather | Variante variant 1; Bauteilnummer Adafruit #3405

### 2 Generic female header - 6

| pins | Form ♀ (female); row single; Paket THT; Beinchen 6; Lochgröße 1.0mm,0.508mm; Beinchenabstand 0.1in (2.54mm)

### 2 Generic male header - 2

| pins | Form ♂ (male); row single; Paket THT; Beinchen 2; Lochgröße 1.0mm,0.508mm; Beinchenabstand 0.1in (2.54mm)

### 1 Generic rounded female

| header - 4 pins | Form ♀ (female rounded); row single; Paket THT; Beinchen 4; Lochgröße 1.0mm,0.508mm; Beinchenabstand 0.1in (2.54mm)

### 1 Generic female header - 2

| pins | Form ♀ (female); row single; Paket THT; Beinchen 2; Lochgröße 1.0mm,0.508mm; Beinchenabstand 0.1in (2.54mm)

### 2 Generic female header - 1

| pins | Form ♀ (female); row single; Paket THT; Beinchen 1; Lochgröße 1.0mm,0.508mm; Beinchenabstand 0.1in (2.54mm)
1 | Green (565nm) LED | Paket 3 mm [THT]; Farbe Green (565nm); leg yes

### 1 Lithium Ion Polymer

| Battery 3.7v 350mAh | Variante 350mAh; Bauteilnummer 2750
3 von 4 | 28.10.2018, 11:43

Amount | Part Type | Properties

### 1 Flora LSM303

| Compass+Accel | Variante variant 1

### 1 MCP3208

| | true; Paket DIP (Dual Inline) [THT]; Beinchen 16; Lochgröße 1.0mm,0.508mm; Chip-Beschriftung MCP3208; Beinchenabstand 300mil

### 1 Generic female header - 4

| pins | Form ♀ (female); row single; Paket THT; Beinchen 4; Lochgröße 1.0mm,0.508mm; Beinchenabstand 0.1in (2.54mm); Bauteilnummer Motor connector

### 1 Generic female header - 3

| pins | Form ♀ (female); row single; Paket THT; Beinchen 3; Lochgröße 1.0mm,0.508mm; Beinchenabstand 0.1in (2.54mm)
2 | 8.2kΩ Resistor | Toleranz ±5%; Paket THT; bands 4; Widerstand 8.2kΩ; Beinchenabstand 400 mil
2 | 680Ω Resistor | Toleranz ±5%; Paket THT; bands 4; Widerstand 680Ω; Beinchenabstand 400 mil
1 | 1kΩ Resistor | Toleranz ±5%; Paket THT; bands 4; Widerstand 1kΩ; Beinchenabstand 400 mil
2 | 0Ω Resistor | Toleranz ±5%; Paket THT; bands 4; Widerstand 0Ω; Beinchenabstand 400 mil
2 | 12kΩ Resistor | Toleranz ±5%; Paket THT; bands 4; Widerstand 12kΩ; Beinchenabstand 400 mil
1 | SPST Switch | Paket switch-spdt; Variante pth

### 1 SN72AHCT

| | true; Paket DIP (Dual Inline) [THT]; Beinchen 14; Lochgröße 0.7mm,0.508mm; Chip-Beschriftung SN72AHCT; Beinchenabstand 300mil

Exported with Fritzing 0.9.3- http://fritzing.org

4 von 4 | 28.10.2018, 11:43

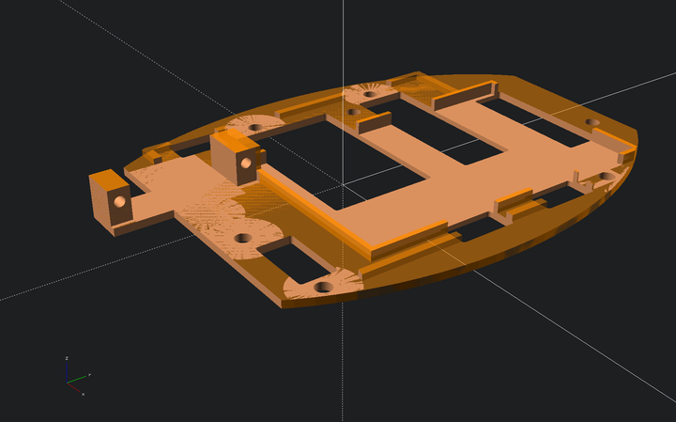
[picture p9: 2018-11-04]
pictures/parts_head_sm.png

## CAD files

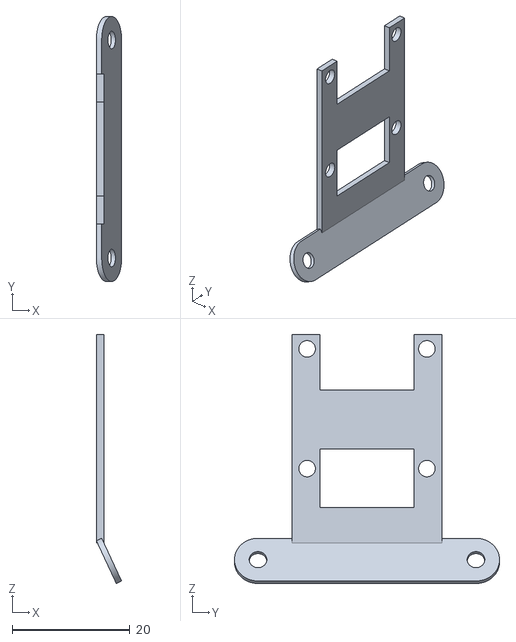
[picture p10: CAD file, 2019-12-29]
printed_parts/hexbug_adapter_2_b_AMG88xx_holder.stl
4.29 x 45.0 x 42.3

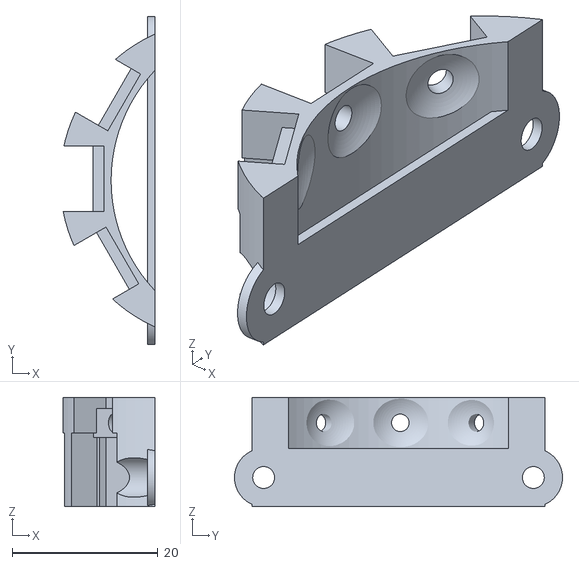
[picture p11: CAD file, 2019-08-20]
printed_parts/hexbug_adapter_2_b_arm_3IR.stl
12.6 x 45.0 x 15.0

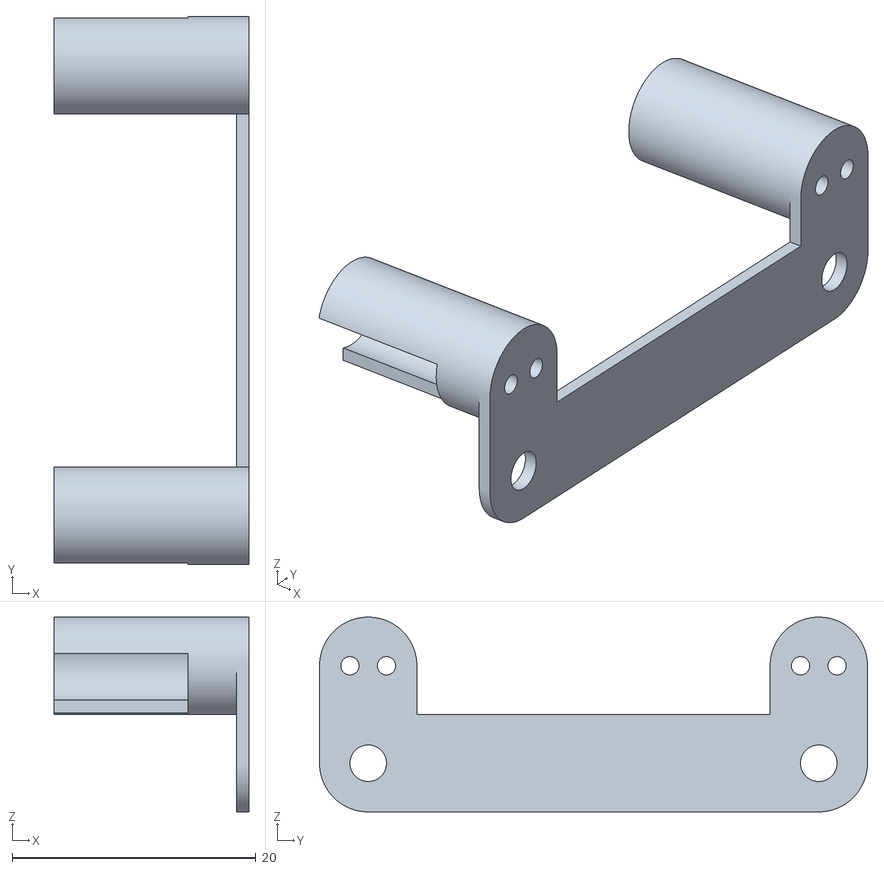
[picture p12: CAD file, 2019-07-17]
printed_parts/hexbug_adapter_2_b_photodiode_shield.stl
16.0 x 45.0 x 16.0

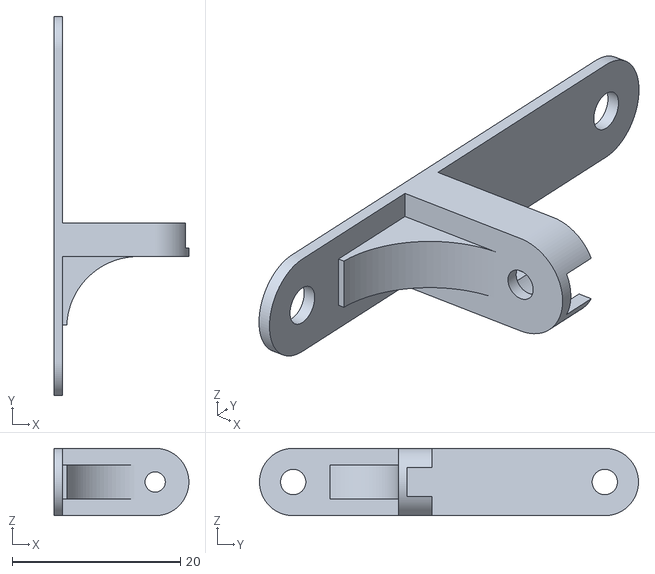
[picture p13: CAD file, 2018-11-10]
printed_parts/hexbug_adapter_2_b_arm.stl
16.0 x 45.0 x 8.00

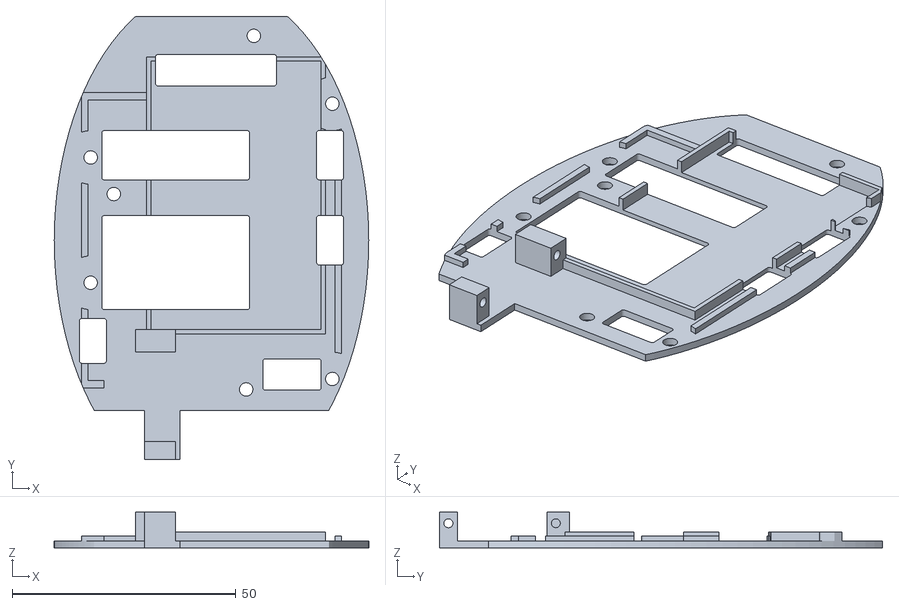
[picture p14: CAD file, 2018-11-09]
printed_parts/hexbug_adapter_2_a_head.stl
70.3 x 99.0 x 8.00

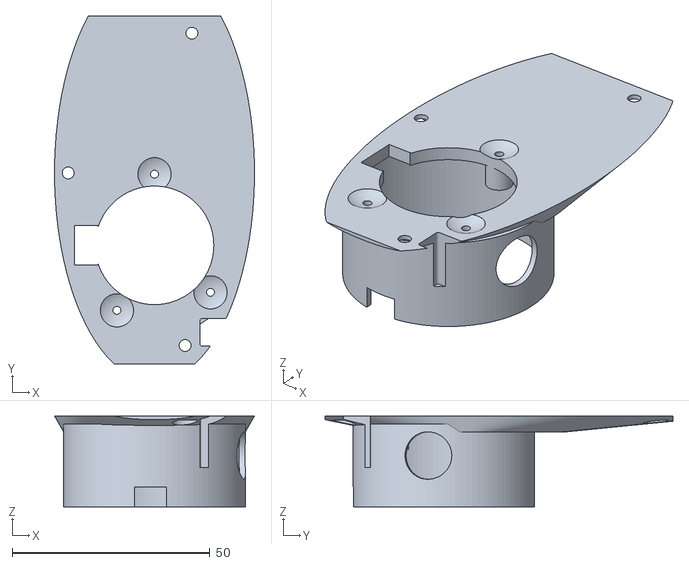
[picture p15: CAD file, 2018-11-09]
printed_parts/hexbug_adapter_2_a_neck.stl
50.6 x 88.0 x 23.0

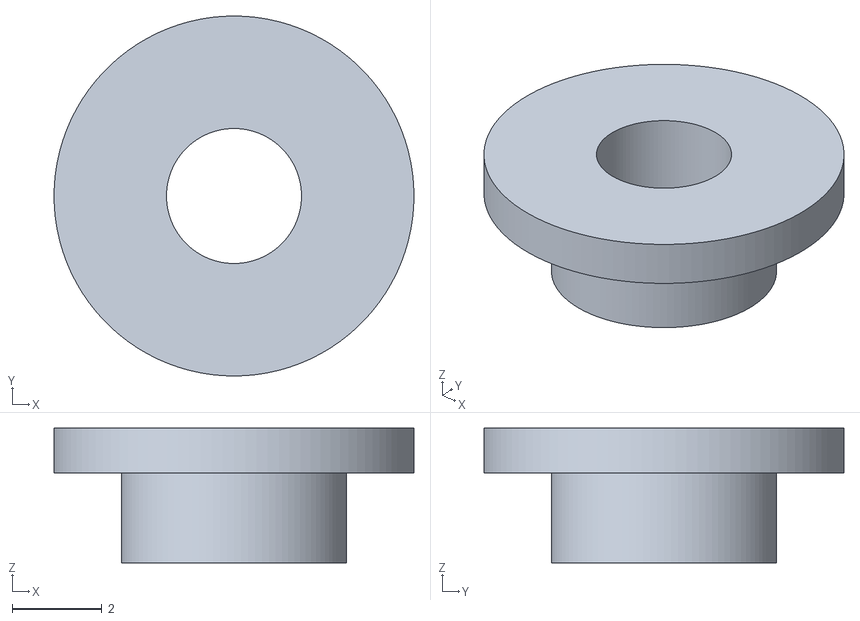
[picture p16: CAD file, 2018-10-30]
printed_parts/hexbug_adapter_1_disc.stl
8.00 x 8.00 x 3.00

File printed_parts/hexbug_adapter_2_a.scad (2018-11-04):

// Visibility flags
showBoard        = 1;
showBattery      = 1;
showServo        = 1;

// Board
board_xyz        = [66.0, 58.0, 1.2];
board_offs       = [-board_xyz[0]/2, -board_xyz[1]/2, 0];
board_rot        = [0, 0, 0];
board_z_angle    = 180;

// Battery
battery_xyz      = [38, 60, 4];
battery_offst    = [-24.5, -40, -0.5];
battery_rot      = [0, 0, 90];

// Servo
/*
servo_xyz        = [23, 21, 13];
servo_xyz2       = [28, 1, 13];
servo_offs2      = [-(servo_xyz2[0] -servo_xyz[0])/2, 2, 0];
*/
servo_xyz        = [20, 19, 8];
servo_xyz2       = [28, 1, 8];
servo_offs2      = [-(servo_xyz2[0] -servo_xyz[0])/2, 4, 0];

servo_rot        = [0, 0, 0];
servo_offs       = [-45, 5, 0];
servo_offs2      = [-(servo_xyz2[0] -servo_xyz[0])/2, 2, 0];

// Base
base_r           = sqrt(pow(board_xyz[0], 2) +pow(board_xyz[1], 2)) /2;
base_scale       = [1.3, 0.8, 1]; // [1.1, 0.9, 1];
base_dz          = 1.5;

post_dz          = 9; //10.0;
post_wall_d      = 1.0;
doPosts          = 0;

board_holes_xyd  =[[2.5, board_xyz[1] -2, 3],
                   [board_xyz[0] -2, board_xyz[1] -2, 3],
                   [14.5, 2, 3],
                   [42.5, 2, 3]];
                   
base_gaps_hulls  = [/*[-5,                   (board_xyz[1]/2 -3), 
                      (board_xyz[0]/2 -18),  (board_xyz[1]/2 -3), 
                     -5,                    -(board_xyz[1]/2 -6),
                      (board_xyz[0]/2 -18), -(board_xyz[1]/2 -6), 3, 20],
                    */ 
                    /*[-(board_xyz[0]/2 -5), (board_xyz[1]/2 -5), 
                     -19,                    (board_xyz[1]/2 -5), 
                     -(board_xyz[0]/2 -5),  -(board_xyz[1]/2 -6),
                     -19,                   -(board_xyz[1]/2 -6), 3, 20],                     
                    */ 
                    // hole for motor connector
                  /*[ 27,                    (board_xyz[1]/2 -5), 
                      (board_xyz[0]/2 +0),   (board_xyz[1]/2 -5), 
                      27,                    (board_xyz[1]/2 -17),
                      (board_xyz[0]/2 +0),   (board_xyz[1]/2 -17), 1, 20],*/
                    
                    [ -27,                   -(board_xyz[1]/2 -5), 
                      -(board_xyz[0]/2 +0),  -(board_xyz[1]/2 -5), 
                      -27,                   -(board_xyz[1]/2 -17),
                      -(board_xyz[0]/2 +0),  -(board_xyz[1]/2 -17), 1, 20],                      
                    
                    [ 24,                    (board_xyz[1]/2 -53), 
                      (board_xyz[0]/2 -19),  (board_xyz[1]/2 -53),  
                      24,                   -(board_xyz[1]/2),
                      (board_xyz[0]/2 -19), -(board_xyz[1]/2), 1, 20],
                    [ 24,                    (board_xyz[1]/2 -5), 
                      (board_xyz[0]/2 -19),  (board_xyz[1]/2 -5),  
                      24,                   -(board_xyz[1]/2 -21),
                      (board_xyz[0]/2 -19), -(board_xyz[1]/2 -21), 1, 20],

                    [ -5,                    (board_xyz[1]/2 -53), 
                      (board_xyz[0]/2 -28),  (board_xyz[1]/2 -53),  
                      -5,                   -(board_xyz[1]/2),
                      (board_xyz[0]/2 -28), -(board_xyz[1]/2), 1, 20],
                    [ -15,                   (board_xyz[1]/2 -5), 
                      (board_xyz[0]/2 -28),  (board_xyz[1]/2 -5),  
                      -15,                  -(board_xyz[1]/2 -21),
                      (board_xyz[0]/2 -28), -(board_xyz[1]/2 -21), 1, 20],

                    [ 35,                    (board_xyz[1]/2 -17), 
                      (board_xyz[0]/2 +8),   (board_xyz[1]/2 -17),  
                      35,                   -(board_xyz[1]/2 -15),
                      (board_xyz[0]/2 +8),  -(board_xyz[1]/2- 15), 1, 20],

                     
                    [-(board_xyz[0]/2 -6),   (board_xyz[1]/2 -0), 
                     -(board_xyz[0]/2 -15),  (board_xyz[1]/2 -0), 
                     -(board_xyz[0]/2 -6),   (board_xyz[1]/2 -5),
                     -(board_xyz[0]/2 -15),  (board_xyz[1]/2 -5), 1, 20]                     
                     ];              

adapt2head_rot   = [0, 0, 90]; 
adapt2head_offs  = [0, 8, 0]; 


// Adapter
adapter_d        = 46;
adapter_wall_d   = 1.5;
adapter_dz       = 21; //20

adapter_gap1_dy  = 7.5;
adapter_gap1_dz  = 5;
adapter_gap1_dx  = 8;

adapt_rim_r      = 6.5;
neck_scale_xy    = [1.1, 2.3]; //[1.2, 1.7];
neck_offs        = [0, 8, 0];  //[0, 4, 0];

// angle, offset from outer circumfence, dz(outer hole), dz(outer wall), dip, hole diameter, 
// outer hole diameter
adapt_holes_ar   =[[ -30, -2.5,  9,  1.5, 1, 2.0, 4.5, 0], 
                   [  50, -3.0,  9,  4.0, 1, 2.0, 4.5, 0], 
                   [ 180, -3.5,  9,  4.0, 1, 2.0, 4.5, 0],
                   
                   [ 230,  7.0, 12, -2.0, 0, 3.0, 6.5, 0],
                   [ 170, 33.0, 12, -2.0, 0, 3.0, 6.5, 0],
                   [  17,  5.0, 12, -2.0, 0, 3.0, 6.5, 1],
                   
                   [  -5,  5.0, 12, -2.0, 0,   0, 6.5, 2]
                   ];
adapt_post_d     = 6;

adapt_collar_dz  = 4; //4
                    
// ----------------------------------------------------------------------------------
// External parts
// ----------------------------------------------------------------------------------
module board0() 
{   
    rotate(board_rot) translate(board_offs) 
    cube(board_xyz);   
}

module board(show=1)
{
    if(show == 1) {
        %color("OliveDrab", 0.7)
        difference() {
            translate([0, 0, post_dz +board_xyz[2]])
            board0();
            rotate([0, 0, board_z_angle])
            for(h = board_holes_xyd) {
                f_hole([h[0], h[1], 0], h[2], 40, board_offs);
            }
        }
    }
}

module battery0(axy=0)
{       
    rotate(battery_rot) translate([0-axy, 0-axy, base_dz]) translate(battery_offst) 
    cube([battery_xyz[0] +2*axy, battery_xyz[1] +2*axy, battery_xyz[2]]);
}

module battery(show=1)
{
    if(show == 1) {
        %color("yellow", 0.3)
        battery0();
    }
}


module servo0() 
{
    rotate(servo_rot) translate([0, 0, base_dz]) translate(servo_offs) 
    group() {
        cube(servo_xyz);
        translate(servo_offs2) 
        cube(servo_xyz2);
    }    
}

module servo(show=1) 
{
    if(show == 1) {
        %color("blue", 0.7) 
        servo0();
    }
}

// ----------------------------------------------------------------------------------
// Functions
// ----------------------------------------------------------------------------------
module f_hole(pos, d, dz, offs=[0,0,0])
{
    translate(offs) {
        rotate(0, [1,0,0]) 
        translate(pos) translate([0, 0, -dz/2])
        cylinder($fn=100, h=dz, r=d/2);
    }
}

module f_post(pos, d, dz, offs=[0,0,0])
{
    translate(offs) {    
        rotate(0, [1,0,0]) translate(pos)
        cylinder($fn=100, h=dz+base_dz, r=d/2);
    }
}

module f_hull_hole(data)
{
    hull() {
        f_hole([data[0], data[1], 0], data[8], data[9]);
        f_hole([data[2], data[3], 0], data[8], data[9]);
        f_hole([data[4], data[5], 0], data[8], data[9]);
        f_hole([data[6], data[7], 0], data[8], data[9]);
    }
}

// ----------------------------------------------------------------------------------
// HEAD
// ----------------------------------------------------------------------------------
module head() 
{
    difference() {
        group() {
            // baseplate
            color("darkorange", 0.5)
            hull() {
                board0();
                base();
            }
            // edge around board
            color("darkorange", 0.5)
            difference() {
                translate([0,0,1.5])
                board0();
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

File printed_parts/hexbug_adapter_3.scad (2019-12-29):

// Visibility flags
showBoard        = 0;
showBattery      = 0;
showServo        = 0;
showboardIR      = 0;

// Board
board_xyz        = [66.0, 58.0, 1.2];
board_offs       = [-board_xyz[0]/2, -board_xyz[1]/2, 0];
board_rot        = [0, 0, 0];
board_z_angle    = 180;

// Battery
battery_xyz      = [38, 60, 4];
battery_offst    = [-24.5, -40, -0.5];
battery_rot      = [0, 0, 90];

// Servo
servo_xyz        = [20, 19, 8];
servo_xyz2       = [28, 1, 8];
servo_rot        = [0, 0, 0];
servo_offs       = [-45, 5, 0];
servo_offs2      = [-(servo_xyz2[0] -servo_xyz[0])/2, 2, 0];

// Base
base_r           = sqrt(pow(board_xyz[0], 2) +pow(board_xyz[1], 2)) /2;
base_scale       = [1.3, 0.8, 1]; // [1.1, 0.9, 1];
base_dz          = 1.5;

post_dz          = 9; //10.0;
post_wall_d      = 1.0;
doPosts          = 0;

board_holes_xyd  =[[2.5, board_xyz[1] -2, 3],
                   [board_xyz[0] -2, board_xyz[1] -2, 3],
                   [14.5, 2, 3],
                   [42.5, 2, 3]];
                   
base_gaps_hulls  = [/*[-5,                   (board_xyz[1]/2 -3), 
                      (board_xyz[0]/2 -18),  (board_xyz[1]/2 -3), 
                     -5,                    -(board_xyz[1]/2 -6),
                      (board_xyz[0]/2 -18), -(board_xyz[1]/2 -6), 3, 20],
                    */ 
                    /*[-(board_xyz[0]/2 -5), (board_xyz[1]/2 -5), 
                     -19,                    (board_xyz[1]/2 -5), 
                     -(board_xyz[0]/2 -5),  -(board_xyz[1]/2 -6),
                     -19,                   -(board_xyz[1]/2 -6), 3, 20],                     
                    */ 
                    // hole for motor connector
                  /*[ 27,                    (board_xyz[1]/2 -5), 
                      (board_xyz[0]/2 +0),   (board_xyz[1]/2 -5), 
                      27,                    (board_xyz[1]/2 -17),
                      (board_xyz[0]/2 +0),   (board_xyz[1]/2 -17), 1, 20],*/
                    
                    [ -27,                   -(board_xyz[1]/2 -5), 
                      -(board_xyz[0]/2 +0),  -(board_xyz[1]/2 -5), 
                      -27,                   -(board_xyz[1]/2 -17),
                      -(board_xyz[0]/2 +0),  -(board_xyz[1]/2 -17), 1, 20],                      
                    
                    [ 24,                    (board_xyz[1]/2 -53), 
                      (board_xyz[0]/2 -19),  (board_xyz[1]/2 -53),  
                      24,                   -(board_xyz[1]/2),
                      (board_xyz[0]/2 -19), -(board_xyz[1]/2), 1, 20],
                    [ 24,                    (board_xyz[1]/2 -5), 
                      (board_xyz[0]/2 -19),  (board_xyz[1]/2 -5),  
                      24,                   -(board_xyz[1]/2 -21),
                      (board_xyz[0]/2 -19), -(board_xyz[1]/2 -21), 1, 20],

                    [ -5,                    (board_xyz[1]/2 -53), 
                      (board_xyz[0]/2 -28),  (board_xyz[1]/2 -53),  
                      -5,                   -(board_xyz[1]/2),
                      (board_xyz[0]/2 -28), -(board_xyz[1]/2), 1, 20],
                    [ -15,                   (board_xyz[1]/2 -5), 
                      (board_xyz[0]/2 -28),  (board_xyz[1]/2 -5),  
                      -15,                  -(board_xyz[1]/2 -21),
                      (board_xyz[0]/2 -28), -(board_xyz[1]/2 -21), 1, 20],

                    [ 35,                    (board_xyz[1]/2 -17), 
                      (board_xyz[0]/2 +8),   (board_xyz[1]/2 -17),  
                      35,                   -(board_xyz[1]/2 -15),
                      (board_xyz[0]/2 +8),  -(board_xyz[1]/2- 15), 1, 20],

                     
                    [-(board_xyz[0]/2 -6),   (board_xyz[1]/2 -0), 
                     -(board_xyz[0]/2 -15),  (board_xyz[1]/2 -0), 
                     -(board_xyz[0]/2 -6),   (board_xyz[1]/2 -5),
                     -(board_xyz[0]/2 -15),  (board_xyz[1]/2 -5), 1, 20]                     
                     ];              

adapt2head_rot   = [0, 0, 90]; 
adapt2head_offs  = [0, 8, 0]; 


// Adapter
adapter_d        = 46;
adapter_wall_d   = 1.5;
adapter_dz       = 21; //20

adapter_gap1_dy  = 7.5;
adapter_gap1_dz  = 5;
adapter_gap1_dx  = 8;

adapt_rim_r      = 6.5;
neck_scale_xy    = [1.1, 2.3]; //[1.2, 1.7];
neck_offs        = [0, 8, 0];  //[0, 4, 0];

// angle, offset from outer circumfence, dz(outer hole), dz(outer wall), dip, hole diameter, 
// outer hole diameter
adapt_holes_ar   =[[ -30, -2.5,  9,  1.5, 1, 2.0, 4.5, 0], 
                   [  50, -3.0,  9,  4.0, 1, 2.0, 4.5, 0], 
                   [ 180, -3.5,  9,  4.0, 1, 2.0, 4.5, 0],
                   
                   [ 230,  7.0, 12, -2.0, 0, 3.0, 6.5, 0],
                   [ 170, 33.0, 12, -2.0, 0, 3.0, 6.5, 0],
                   [  17,  5.0, 12, -2.0, 0, 3.0, 6.5, 1],
                   
                   [  -5,  5.0, 12, -2.0, 0,   0, 6.5, 2]
                   ];
adapt_post_d     = 6;

adapt_collar_dz  = 4; //4
                    
// ----------------------------------------------------------------------------------
// External parts
// ----------------------------------------------------------------------------------
module board0() 
{   
    rotate(board_rot) translate(board_offs) 
    cube(board_xyz);   
}

module board(show=1)
{
    if(show == 1) {
        %color("OliveDrab", 0.7)
        difference() {
            translate([0, 0, post_dz +board_xyz[2]])
            board0();
            rotate([0, 0, board_z_angle])
            for(h = board_holes_xyd) {
                f_hole([h[0], h[1], 0], h[2], 40, board_offs);
            }
        }
    }
}

module battery0(axy=0)
{       
    rotate(battery_rot) translate([0-axy, 0-axy, base_dz]) translate(battery_offst) 
    cube([battery_xyz[0] +2*axy, battery_xyz[1] +2*axy, battery_xyz[2]]);
}

module battery(show=1)
{
    if(show == 1) {
        %color("yellow", 0.3)
        battery0();
    }
}


module servo0() 
{
    rotate(servo_rot) translate([0, 0, base_dz]) translate(servo_offs) 
    group() {
        cube(servo_xyz);
        translate(servo_offs2) 
        cube(servo_xyz2);
    }    
}

module servo(show=1) 
{
    if(show == 1) {
        %color("blue", 0.7) 
        servo0();
    }
}

// - - - - - - - - - - - - - - - - - - - - - - - - - - - - - - - - - - - - - - - - - 
module IRSensor_holes(dx) 
{
    translate([15,dx/2,-15])
    group() {
        cylinder($fn=100, h=20, r=1.2);
        translate([0,0,9])
        sphere(6, $fn=100);
    }
}

module IRSensor(hole=0) 
{
    dx1 = 8.5 +0.5;  // 8.5
    dx2 = 10. +0.53;  //10.0
    dy  = 6.3;
    difference() {
        group() {
            translate([0, (dx1-dx2)/2, 1])
            cube([13.6, dx2, dy -1.0]);   
            if(hole == 0) 
                cube([23.8, dx1, 1.0]);   
            else     
                cube([23.8, dx1, dy]);   
        }
        if(hole == 0) 
            IRSensor_holes(dx1);
        else {
            translate([13, (dx1-dx2)/2, 0])
            cube([4,dx2, 1.5]);
        }
    }
    if(hole == 1) 
        IRSensor_holes(dx1);
}

module boardIR0(hole) 
{   
    angx = 0; //-25;
    angz = 30; 
    offx = 2;
    offy = 8;
    
    prm  = [[offx, -offy, angx,  angz],
            [0,        0, angx,     0],
            [offx,  offy, angx, -angz]];

    for(p=prm) {
        translate([p[0], p[1], 0]) rotate([0, p[2], p[3]])
        group() {
            rotate([0,-90,0]) translate([0,-8.5/2,5]) 
            IRSensor(hole);
        }
    }
}

module boardIR(show=1, hole=0)
{
    if(show == 1) {
        translate([-54,-0,-2])
        color("OliveDrab", 0.2)
        boardIR0(hole);
    }
}


// ----------------------------------------------------------------------------------
// Functions
// ----------------------------------------------------------------------------------
module f_hole(pos, d, dz, offs=[0,0,0])
{
    translate(offs) {
        rotate(0, [1,0,0]) 
        translate(pos) translate([0, 0, -dz/2])
        cylinder($fn=100, h=dz, r=d/2);
    }
}

module f_post(pos, d, dz, offs=[0,0,0])
{
    translate(offs) {    
        rotate(0, [1,0,0]) translate(pos)
        cylinder($fn=100, h=dz+base_dz, r=d/2);
    }
}

module f_hull_hole(data)
{
    hull() {
        f_hole([data[0], data[1], 0], data[8], data[9]);
        f_hole([data[2], data[3], 0], data[8], data[9]);
        f_hole([data[4], data[5], 0], data[8], data[9]);
        f_hole([data[6], data[7], 0], data[8], data[9]);
    }
}
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

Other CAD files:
printed_parts/hexbug_adapter_2_b.scad

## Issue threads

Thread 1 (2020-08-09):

add functionality to subcriber robotling telemetry messages from broker

GreenCap95, 2020-08-09:

teuler, 2020-08-09:
Hi, not sure what your suggest/request is. Could you provide some details?

GreenCap95, 2020-08-09:
Hello,

Unfortunately I realized to late that this doesn’t belong there. I’m sorry for that.

Git and GitHub is still rather new to me and and I was wondering whether I could
Organize my To-do’s that way.

By the way, thanks for this great project! I build six robotlings last year, which are now used for education purposes at my university.

Sincerely

Daniel Mansfeldt

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

teuler, 2020-08-10:
Hi Daniel,

thanks for your message and for liking the project.

Best
Thomas

Closed 2020-08-21.

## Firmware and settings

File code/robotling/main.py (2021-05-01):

# ----------------------------------------------------------------------------
# main.py
# Main program; is automatically executed after reboot.
#
# For decription, see `hexbug.py`
#
# The MIT License (MIT)
# Copyright (c) 2019 Thomas Euler
# 2018-12-22, reorganised into a module with the class `Hexbug` and a simpler
#             main program file (`main.py`). All hardware-related settings
#             moved to separate file (`hexbug_config-py`)
# 2018-12-28, adapted to using the new `spin_ms()` function to keep the
#             robotling board updated; does not require a Timer anymore.
#             For details, see `robotling.py`.
# 2019-04-07, added new "behaviour" (take a nap)
# 2019-07-13, added new "behaviour" (find light)
#             `hexbug_config.py` reorganised and cleaned up
# 2019-07-24, added "memory" to turn direction (experimental)
# 2019-08-19, in case of an uncaught exception, it tries to send a last
#             MQTT message containing the traceback to the broker
# 2021-04-29, Some refactoring; configuration parameters now clearly marked
#             as such (`cfg.xxx`)
#
# ----------------------------------------------------------------------------
from hexbug import *

# ----------------------------------------------------------------------------
def main():
  # Setup the robot's spin function
  r.spin_ms(period_ms=cfg.TM_PERIOD, callback=r.housekeeper)

  # Angle the IR sensor towards floor in front
  r.ServoRangingSensor.angle = cfg.SCAN_DIST_SERVO
  r.spin_ms(100)

  # Loop ...
  print("Entering loop ...")
  try:
    try:
      lastTurnDir = 0
      round = 0

      while True:
        try:
          r.onLoopStart()

          if r.onHold:
            # Some problem was detected (e.g. robot tilted etc.), skip all
            # the following code
            lastTurnDir = 0
            continue

          # Sometines just look around
          if random.randint(1,1000) <= cfg.DO_LOOK_AROUND:
            r.lookAround()
            continue

          # Sometines sleep
          if random.randint(1,1000) <= cfg.DO_TAKE_NAPS:
            r.sleepLightly()
            continue

          # If blob following behaviour is activated, check for blobs every
          # 10th round
          if cfg.DO_FOLLOW_BLOB and round % 20 == 0:
            r.lookAtBlob(cfg.BLOB_MIN_AREA, cfg.BLOB_MIN_PROB)
            continue

          # Check if obstacle or cliff
          r.onTrouble = r.scanForObstacleOrCliff()

          # Act on sensor data ...
          if r.onTrouble == 0:
            # No reason to stop, therefore walk
            r.state = STATE_WALKING
            r.MotorWalk.speed = cfg.SPEED_WALK
            if not r.turnStats == 0:
              # Slowly "forget" the unsuccessful turn direction
              r.turnStats += MEM_DEC if r.turnStats < 0 else -MEM_DEC
            lastTurnDir = 0

          elif r.onTrouble < 0:
            # Obstacle detected -> Stop, turn in a random direction to check
            # (in the next spin) again for obstacles
            r.state = STATE_OBSTACLE
            r.MotorWalk.speed = 0
            r.spin_ms(50)
            lastTurnDir = r._nextTurnDir(lastTurnDir)
            r.MotorTurn.speed = cfg.SPEED_TURN *lastTurnDir
            r.spin_ms(cfg.SPEED_TURN_DELAY)
            r.MotorTurn.speed = 0

          else:
            # Cliff detected -> Stop, walk back a tad, turn in a random
            # direction to check (in the next spin) again for obstacles
            r.state = STATE_CLIFF
            r.MotorWalk.speed = 0
            #r.spin_ms(500)
            r.spin_ms(100)
            r.MotorWalk.speed = -cfg.SPEED_WALK
            r.spin_ms(cfg.SPEED_BACK_DELAY)
            r.MotorWalk.speed = 0
            lastTurnDir = r._nextTurnDir(lastTurnDir)
            r.MotorTurn.speed = cfg.SPEED_TURN *lastTurnDir
            r.spin_ms(cfg.SPEED_TURN_DELAY*2)
            r.MotorTurn.speed = 0

          # If compass is used and a heading was chosen (because of cliff or
          # obstacle), save this as new target heading
          if r.onTrouble != 0 and cfg.DO_WALK_STRAIGHT:
            r._targetHead = r.Compass.getHeading()

        finally:
          # Make sure the robotling board get updated at least once per loop
          r.spin_ms()
          round += 1

    except KeyboardInterrupt:
      print("Loop stopped.")

  finally:
    # Make sure that robot is powered down
    r.ServoRangingSensor.off()
    r.powerDown()
    r.printReport()

# ----------------------------------------------------------------------------
# Create instance of HexBug, derived from the Robotling class
r = HexBug(cfg.MORE_DEVICES)

# Call main
if __name__ == "__main__":
  try:
    main()
  except Exception as e:
    # Create an in-memory file-like string object (`sIO`) to accept the
    # exception's traceback (`sys.print_exception` requires a file-like
    # object). This traceback string is then converted into a dictionary
    # to be sent as an MQTT message (if telemetry is activate)
    if cfg.SEND_TELEMETRY and r._t._isReady:
      import sys, uio
      sIO = uio.StringIO()
      sys.print_exception(e, sIO)
      r._t.publishDict(KEY_RAW, {KEY_DEBUG: str(sIO.getvalue())})
    # Re-raise the exception such that it becomes also visible in the REPL
    raise e

# ----------------------------------------------------------------------------

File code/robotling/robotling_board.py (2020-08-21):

# ----------------------------------------------------------------------------
# robotling_board.py
# Global definitions for robotling board.
#
# The MIT License (MIT)
# Copyright (c) 2018 Thomas Euler
# 2018-09-13, v1
# 2018-12-22, v1.1 - pins for M4 feather express added
# 2020-01-01, v1.2 - pins for hexapod robotling added
# 2020-08-21, v1.3 - refactoring for `robotling_lib`
#
# ----------------------------------------------------------------------------
from micropython import const
from robotling_board_version import BOARD_VER
from robotling_lib.platform.platform import platform

__version__ = "0.1.3.0"

SPI_FRQ   = const(4000000)
I2C_FRQ   = const(400000)

# I2C devices, maximal clock frequencies:
# AMG88XX (Infrared Array Sensor “Grid-EYE”)  <= 400 KHz
# VL6180X (Time of Flight distance sensor)    <= 400 KHz
# CMPS12  (Compass)                           <= 400 KHz
# LSM303  (Compass)                           100, 400 KHz
# LSM9DS0 (Compass)                           100, 400 KHz

# ----------------------------------------------------------------------------
# Robotling board connections/pins
#
if platform.ID == platform.ENV_ESP32_UPY:
  import robotling_lib.platform.esp32.board_huzzah32 as board

  # SPI -----------------
  SCK        = board.SCK
  MOSI       = board.MOSI
  MISO       = board.MISO
  CS_ADC     = board.D4
  if BOARD_VER >= 200:
    CS_ADC1  = board.D26
    CS_ADC2  = board.D25

  # I2C -----------------
  SCL        = board.SCL
  SDA        = board.SDA
  if BOARD_VER >= 200:
    D_I2C    = board.D14

  # UART  ---------------
  TX         = board.TX
  RX         = board.RX
  BAUD       = 230400 #115200

  # DC Motors -----------
  if BOARD_VER < 200:
    A_ENAB   = board.D26
    A_PHASE  = board.D14
    B_ENAB   = board.D21
    B_PHASE  = board.D25

  # DIO -----------------
  if BOARD_VER == 100:
    NEOPIX   = board.D15      # Connect Neopixel to DIO #0
    DIO0     = board.D27
    DIO1     = board.LED
    DIO2     = board.D33
    DIO3     = board.D15
  elif BOARD_VER >= 110 and BOARD_VER < 200:
    NEOPIX   = board.D15      # -> Neopixel connector
    DIO0     = board.D27
    DIO1     = board.LED
    DIO2     = board.D33
    DIO3     = board.D32
  elif BOARD_VER > 200:
    BLUE_LED = board.D32      # -> also DIO3
    NEOPIX   = board.D15      # -> Neopixel connector
    DIO0     = board.D27
    DIO1     = board.LED
    DIO2     = board.D33
    DIO3     = board.D32

  # Other ---------------
  ENAB_5V    = board.D16
  RED_LED    = board.LED
  ADC_BAT    = board.BAT

  # Note 1: The ESP32 MicroPython port currently supports only one frequency
  # for all PWM objects. Servos usually expect 50 Hz, but to run the DC motors
  # somewhat smoother, a higher frequency can be tested
  # Note 2: DIO uses now the RMT feature of the ESP32, which offers an
  # alternative to the standard PWM with more flexible frequencies
  SERVO_FRQ  = 50 #250
  MOTOR_FRQ  = SERVO_FRQ
  MOTOR_A_CH = 0
  MOTOR_B_CH = 1


if platform.ID == platform.ENV_ESP32_TINYPICO:
  import platform.esp32.board_tinypico as board

  # SPI -----------------
  SCK        = board.SCK
  MOSI       = board.MOSI
  MISO       = board.MISO

  # I2C -----------------
  SCL        = board.SCL
  SDA        = board.SDA

  # UART  ---------------
  TX         = board.D18
  RX         = board.D19
  BAUD       = 230400 #115200

  # Other ---------------
  DS_CLOCK   = board.DSCL
  DS_DATA    = board.DSDT
  DS_POWER   = board.DSPW

  GREEN_LED  = board.D27
  SERVOS_OFF = board.D25
  BUZZER     = board.D15
  ADC_POT    = board.D32
  ADC_BAT    = board.D33
  KEYPAD_POW = board.D26

  SERVO_FRQ   = 50 #250


elif platform.ID == platform.ENV_CPY_SAM51:
  import board

  SCK     = board.SCK
  MOSI    = board.MOSI
  MISO    = board.MISO
  CS_ADC  = board.A5

  SCL     = board.SCL
  SDA     = board.SDA

  A_ENAB  = board.A3
  # The M4 express feather does not allow PWM with pin A0, therefore to use
  # robotling boards <= v1.2 requires to solder a bridge between the pins A0
  # and A3.
  A_PHASE = board.D5
  B_ENAB  = board.D4
  B_PHASE = board.A1

  ENAB_5V = board.RX
  RED_LED = board.D13

  ADC_BAT = board.VOLTAGE_MONITOR

  if BOARD_VER == 100:
    '''
    NEOPIX  = board.D9  #D15 # Connect Neopixel to DIO #0
    '''
    NEOPIX  = board.NEOPIXEL
    DIO0    = board.D11
    DIO1    = board.D13
    DIO2    = board.D10
    DIO3    = board.D9

  elif BOARD_VER >= 110:
    '''
    NEOPIX  = board.D9  #D15 # -> Neopixel connector
    '''
    NEOPIX  = board.NEOPIXEL
    DIO0    = board.D11
    DIO1    = board.D13
    DIO2    = board.D10
    DIO3    = board.D6

  # The M4 allows for different frequencies for PWM channels; `MOTOR_A_CH`
  # and `MOTOR_B_CH` are -1 because the RMT feature of the ESP32 is not
  # available not nescessary here
  SERVO_FRQ  = 50
  MOTOR_FRQ  = 150
  MOTOR_A_CH = -1
  MOTOR_B_CH = -1
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

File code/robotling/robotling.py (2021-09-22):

# ----------------------------------------------------------------------------
# robotling.py
# Definition of the class `Robotling`, which subsumises all functions of the
# robotling board.
#
# The MIT License (MIT)
# Copyright (c) 2018-2021 Thomas Euler
# 2018-09-13, v1
# 2018-11-10, v1.1, Compatible to Boris Lovosevic's MicroPython ESP32 port
# 2018-12-22, v1.2, Class `Robotling` now more restricted to the board-
#                   related functions
# 2018-12-28, v1.3, Added `spin_ms()`, which needs to be called once per loop
#                   and instead of `sleep_ms()` to keep board updated. This
#                   solution is superior to the use of a timer, because a) it
#                   is deterministic (avoids randomly interrupting the program
#                   flow and, hence, inconsistencies) and b) makes the code
#                   compatible to CircuitPython, which does not (yet?) support
#                   timers.
# 2019-01-01, v1.4, vl6180x time-of-flight distance sensor support added
# 2019-01-20, v1.5, DotStar feather support added
# 2018-03-25, v1.6, deepsleep/lightsleep support for ESP32
# 2019-05-23        LSM9DS0 accelerometer/magnetometer/gyroscope support added
# 2019-07-13, v1.7, `hexbug_config.py` reorganised and cleaned up
# 2019-07-25,       Added `wlan` to the list of possible devices
# 2019-08-03, v1.8, AMG88XX (8x8 IR camera) driver added
#                   `I2C_FRQ` increased; from specs this should be compatible
#                   with all currently supported I2C devices
# 2019-12-21, v1.9, Micropython 1.12.0
#                   - hardware I2C bus option added
#                   - native code generation added (needs MicroPython >=1.12)
#                   Define PWM frequencies for servos and DC motors to account
#                   for the fact the the ESP32 port supports only a single
#                   frequency for all PWM pins (see `robotling_board.py`)
# 2020-08-21, v1.9, Refactoring for `robotling_lib`
# 2020-11-15, v1.9, Further refactoring (platform based on language not board)
# 2021-04-18, v1.9, Small bug fixes, works w/ MicroPython v1.14
# 2021-04-21, v1.9, Now uses `RobotlingBase`
# 2021-04-29, v1.9, Some refactoring
#
# Open issues:
# - NeoPixels don't yet quite as expected with the LoBo ESP32 MicroPython
# - LSM303: While accelerometer readings are fine, computing a clear heading
#   from the magnetometer does yet work. Potentially a hardware problem with
#   the prototype board. In any case, the compass does not yet work.
#   With the CMPS12 module, the compass works just fine.
# ----------------------------------------------------------------------------
import gc
import array
import robotling_lib.robotling_board as rb
import robotling_lib.driver.drv8835 as drv8835
from robotling_board_version import BOARD_VER
from robotling_lib.robotling_base import RobotlingBase

from robotling_lib.platform.platform import platform as pf
if pf.languageID == pf.LNG_MICROPYTHON:
  import robotling_lib.platform.esp32.board_huzzah32 as board
  from robotling_lib.platform.esp32.dio import DigitalOut
  from robotling_lib.platform.esp32.aio import AnalogIn
  from robotling_lib.platform.esp32.busio import  I2CBus
  from robotling_lib.platform.esp32.neopixel import NeoPixel
  from machine import deepsleep, lightsleep
  import time
elif pf.languageID == pf.LNG_CIRCUITPYTHON:
  import board
  from robotling_lib.platform.circuitpython.dio import DigitalOut
  from robotling_lib.platform.circuitpython.aio import AnalogIn
  from robotling_lib.platform.circuitpython.busio import I2CBus
  from robotling_lib.platform.circuitpython.neopixel import NeoPixel
  import robotling_lib.platform.circuitpython.time as time
else:
  print("ERROR: No matching hardware libraries in `platform`.")

__version__ = "0.1.9.4"

# ----------------------------------------------------------------------------
class Robotling(RobotlingBase):
  """Robotling main class.

  Objects:
  -------
  - power5V        : on(), off()
  - Compass        : see sensors.compass*.py

  Methods:
  -------
  - update()
    Update onboard devices (Neopixel, analog sensors, etc.). Call frequently
    to keep sensors updated and NeoPixel pulsing!
  - sleepLightly(), sleepDeeply()

  Properties:
  ----------
  - Battery_V      : battery voltage [V]
  - NeoPixelRGB    : get and set color (assign r,g,b tuple)
  - ID             : GUID of board/feather

  Internal objects:
  ----------------
  - _LSM303        : magnetometer/accelerometer driver (if available)
  - _LSM9DS0       : accelerometer/magnetometer/gyroscope driver (if available)
  - _VL6180X       : time-of-flight distance sensor driver (if available)
  - _AMG88XX       : GRID-Eye IR 8x8 thermal camera driver (if available)
  - _DS            : DotStar array feather (if available)
  - _motorDriver   : 2-channel DC motor driver
  """

  def __init__(self, devices=[]):
    """ Additional onboard components can be listed in `devices` and, if known,
        will be initialized
    """
    si = pf.sysInfo
    print("Robotling (board v{0:.2f}, software v{1}) w/{2} {3} ({4})"
          .format(BOARD_VER/100, __version__, pf.language, si[2], si[0]))
    print("Initializing ...")

    # Initialize base object
    super().__init__(neoPixel=True, MCP3208=True)
    print("[{0:>12}] {1:35}".format("GUID", self.ID))

    # Initialize on-board (feather) hardware
    self._adc_battery = AnalogIn(rb.ADC_BAT)
    if BOARD_VER >= 120:
      self.power5V = DigitalOut(rb.ENAB_5V, value=True)

    # Initialize motor driver
    self._motorDriver = drv8835.DRV8835(
        drv8835.MODE_PH_EN, rb.MOTOR_FRQ,
        rb.A_ENAB, rb.A_PHASE, rb.B_ENAB, rb.B_PHASE
      )

    # Get hardware I2C bus (#0)
    self._I2C = I2CBus(freq=rb.I2C_FRQ, scl=rb.SCL, sda=rb.SDA, scan=True)

    # Reset potential "device" objects
    self._devices = devices
    self._VL6180X = None
    self._DS = None
    self._AMG88XX = None
    self.Compass = None
    self.Camera = None

    # Initialize further devices depending on the selected onboard components
    # (e.g. which type of magnetometer/accelerometer/gyro, etc.)
    if "lsm303" in devices:
      # Magnetometer and accelerometer break-out, import drivers and
      # initialize lsm303 and respective compass instance
      gc.collect()
      from robotling_lib.sensors import compass
      from robotling_lib.driver import lsm303
      gc.collect()
      self._LSM303 = lsm303.LSM303(self._I2C)
      self.Compass = compass.Compass(self._LSM303)

    if "lsm9ds0" in devices:
      # Magnetometer/accelerometer/gyroscope break-out, import drivers and
      # initialize lsm9ds0 and respective compass instance
      gc.collect()
      from robotling_lib.sensors import compass
      from robotling_lib.driver import lsm9ds0
      gc.collect()
      self._LSM9DS0 = lsm9ds0.LSM9DS0(self._I2C)
      self.Compass = compass.Compass(self._LSM9DS0)
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

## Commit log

2018-10-30 First release
    [hexbug_adapter_1_disc.stl, hexbug_adapter_1_head.stl, hexbug_adapter_1_neck.stl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]
2018-10-30 Update board v1.2
    [robotling_version1_2.fzz]
2018-11-04 3D parts updated
    [hexbug_adapter_1_head.stl, hexbug_adapter_1_neck.stl, hexbug_adapter_2_a.scad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]
2018-11-10 Sensor arm improved, improved code compatibility
    [hexbug_adapter_2_b.scad, hexbug_adapter_2_b_arm.stl]
2019-01-12 Bug fixes and updates
    - more devices
    - M4 Feather Express works as well
    [hexbug.py, hexbug_config.py, main.py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]
2019-04-13 Board version 1.3 w/Gerber files
    [robotling_version1_3.fzz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]
2019-05-18 Gerber files
    [robotling_version1_2_contour.gm1, robotling_version1_2_copperBottom.gbl, robotling_version1_2_copperTop.gtl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]
2019-07-17 Photodiode shield
    [hexbug_adapter_2_b.scad, hexbug_adapter_2_b_photodiode_shield.stl]
2019-07-18 Photodiode circuit added
2019-07-25 WLAN as possible device
2019-08-20 Another part
    [hexbug_adapter_2_b_arm_3IR.stl]
2019-12-29 Thermal camera plus small code changes
2019-12-29 New pictures and parts
    [hexbug_adapter_2_b_AMG88xx_holder.stl, hexbug_adapter_3.scad]
2020-08-21 Major refactoring, all drivers etc moved to `robotling_lib`
    See release notes.
2020-08-21 Fix problem with importing robotling_board
    [hexbug.py, hexbug_config.py, robotling.py]
2020-08-22 Bug fixes in `blob.c` and the GUI library
    [front_pygame.py]
2020-08-22 Bug fixes related to IR cam blob detection
    [hexbug_config.py]
